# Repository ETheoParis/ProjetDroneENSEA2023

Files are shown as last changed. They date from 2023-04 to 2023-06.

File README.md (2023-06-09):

# ProjetDroneENSEA2023

I. Introduction :

Nous avons choisi de constituer un groupe de 5 personnes pour asservir et concevoir le PCB d'un drone. La structure en impression 3D nous a été fourni, nous nous sommes donc penchés sur la partie électronique et informatique.
Selon le dictionnaire Larousse, un drone "est un petit avion télécommandé utilisé pour des tâches diverses". Dans notre cas, le cahier des charges impose que notre drone puisse décoller, voler de manière rectiligne et atterrir après avoir volé pendant x mètres. 
Pour satisfaire le cahier des charges, nous avons divisé le travail entre les membres du groupe. Jack Du, Nesrine Mathlouthi, Cassandre Chandelier et Théo Paris se sont occupés de l’asservissement et du programme informatique pendant que Fannie Bichemin a réalisé le schématique  et l’éditeur de PCB ainsi que la soudure des composants.

I.1 Organisation :

Nous avons choisi de créer un groupe Messenger pour présenter nos avancées individuelles en dehors des séances de projet. Nous présentions nos recherches et les idées que nous avions pour résoudre les problèmes que nous avons rencontrés. De plus, nous avons réalisé dès la première séance un diagramme de Gantt pour suivre l’évolution de nos tâches respectives et du projet dans sa globalité. 

Que ce soit pour la surveillance de territoires, l'inspection de bâtiments, la cartographie de zones difficiles d'accès ou encore la livraison de colis, les drones sont devenus indispensables pour de nombreuses entreprises. Il s’agit de petits avions télécommandés utilisés pour des tâches diverses. (Larousse)

Notre objectif est d’asservir et de concevoir le PCB d’un drone quadcoptère dont la structure nous a été fournie. Nous veillerons à respecter le cahier des charges suivant : 
- Véhicule autonome
- Processeur sur carte-mère
- Pas de contrôle à distance  
- Code embarqué : C sur STM32
- Avancer, décoller
- Avancer "droit" puis de 10 m.

____________________________________________________________________________________________________________________________________________________________

I.1 Répartition des tâches :

Afin de satisfaire le cahier des charges, nous avons constitué un groupe de cinq personnes formé par :
- Fannie Bichemin (Hardware)
- Cassandre Chandelier, Jack Du, Nesrine Mathlouthi et Théo Paris (Asservissement et Software)

En ce qui concerne les livrables tels que le rapport et la soutenance, ils ont été complétés par les membres en expliquant les parties qui les concernent. 
____________________________________________________________________________________________________________________________________________________________

I.2 Organisation :

Afin de travailler facilement, nous avons choisi de créer un groupe Messenger. Ce dernier nous a permis de partager nos avancées individuelles en dehors des séances de projet. Nous présentions nos recherches et idées que nous avions pour résoudre les problèmes que nous avons rencontrés. De plus, nous avons réalisé dès la première séance un diagramme de Gantt pour suivre l’évolution de nos tâches respectives et du projet dans sa globalité. 

____________________________________________________________________________________________________________________________________________________________
____________________________________________________________________________________________________________________________________________________________

II.Hardware

II. Réalisation :

II.1 Le PCB :

Afin de réaliser le PCB, nous avons commencé par faire le schématique. 
Nous avons tout d’abord rassemblé toutes les datasheets et nous avons dessiné un diagramme pour visualiser le placement des composants (Cf figure.1 ) ainsi que le nombre de composants nécessaires pour concevoir le PCB. Par la suite, nous avons regardé les schémas présents dans les datasheets pour connaitre la valeurs des résistances et des condensateurs à placer autour du régulateur et des blocs moteurs. Nous nous sommes également aidés du TD concernant KiCad pour trouver les valeurs des résistances à placer autour de la carte STM32. 

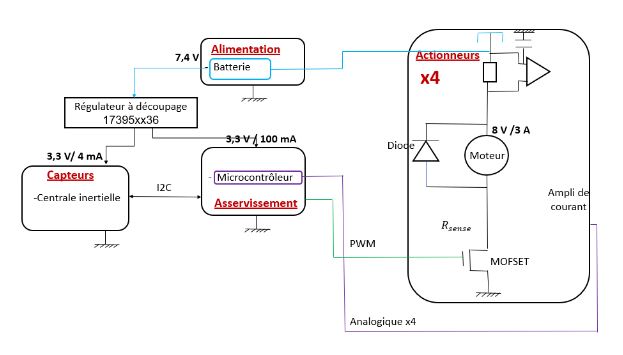
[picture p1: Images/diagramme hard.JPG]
diagramme hardware


Figure 1: Diagramme qui représente les différents éléments électroniques utilisés 

Nous avons donc abouti au schématique suivant :

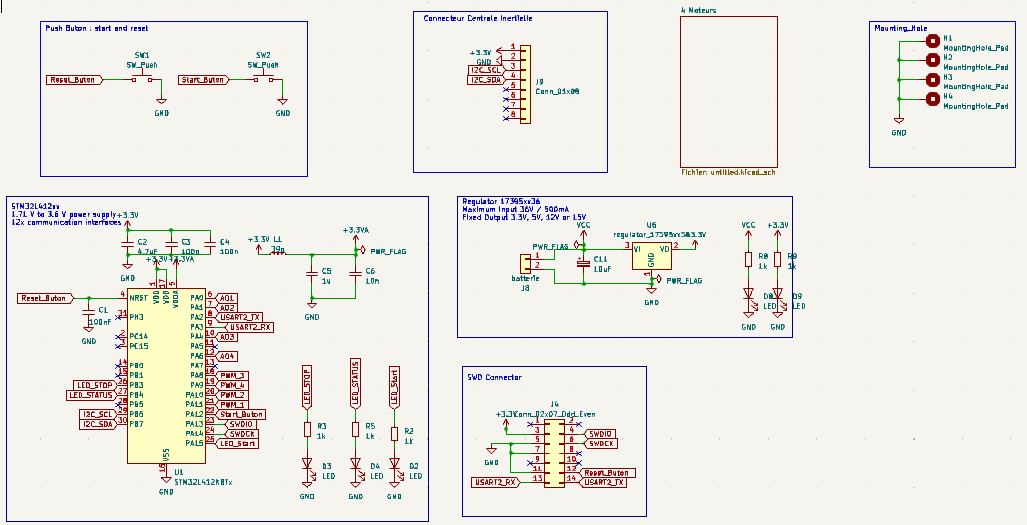
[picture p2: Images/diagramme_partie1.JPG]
schématique1


	Figure 2.a : Première partie du schématique du projet

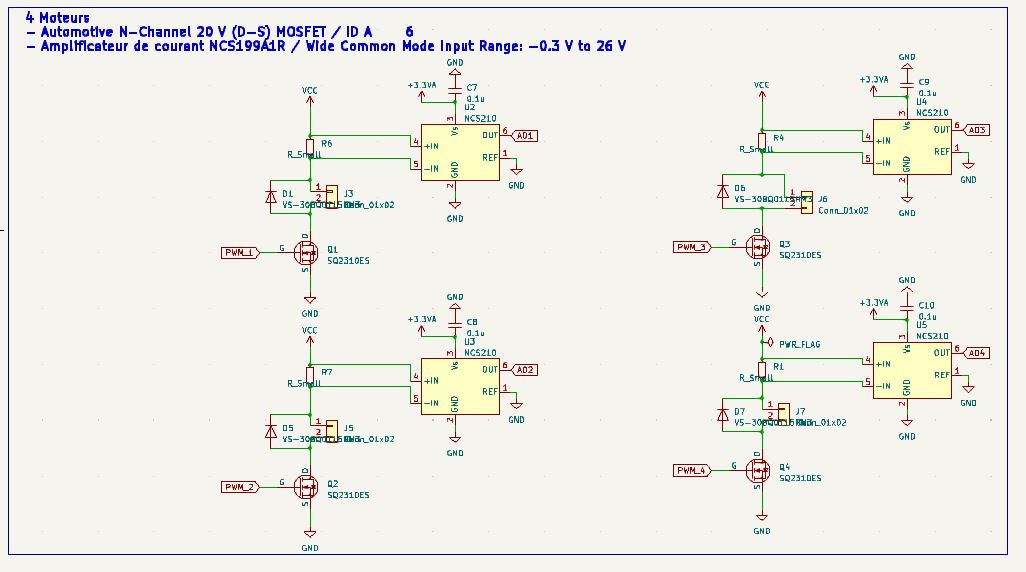
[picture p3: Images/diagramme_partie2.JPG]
diagramme partie2


Figure 2.b : Deuxième partie du schématique du projet (les moteurs)

Le schématique comporte plusieurs parties: 

-La carte STM32
-Les boutons poussoirs
-La centrale inertielle
-La cellule de régulation
-Le connecteur SWD
-La cellule des 4 moteurs 
 
Pour ajouter les résistances, les condensateurs et les bobines, nous avons regardé les montages présentés dans les datasheets. Ces montages nous permettent de connaître le nombre et la valeur des résistances et des condensateurs à placer autour des composants centraux”.
Les problèmes rencontrés sont : 
Le choix des empreintes (faire attention au numéro à prendre le numéro 0603 et “l’option” handsolder pour faciliter la soudure ; Créer des empreintes si elles n’existent pas déjà dans les librairies en faisant surtout attention aux distances entre les pads ainsi que les contours). 
Ne pas oublier de mettre des power flag.
Les empreintes des condensateurs en fonction de leurs valeurs. 

Par la suite, nous avons placé les composants sur l’éditeur PCB. Il a fallu faire en sorte que la taille et la forme du PCB soient adaptées à l’emplacement prévu sur la base du drone imprimée en 3D. 

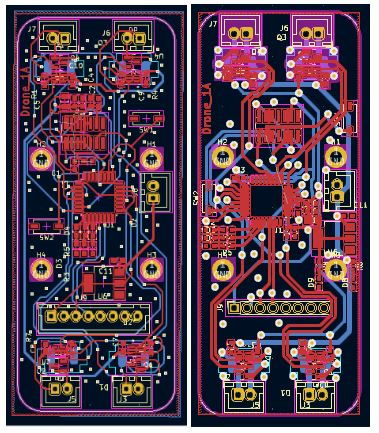
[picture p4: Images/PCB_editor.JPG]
editor PCB


Figure 2.b : PCB 

Remarques:

Le PCB de gauche est la version qui aurait dû être fabriquée par le procédé “traditionnel”.  
Le PCB de droite est celui qui a été refait par Monsieur Papazouglou car il fallait modifier la manière de placer les composants puisque le PCB a été fabriqué par le système de gravure. 

Les problèmes rencontrés sont: 
Faire en sorte de relier de la manière la plus courte possible les pads entre eux. 

____________________________________________________________________________________________________________________________________________________________

Les choses à retenir:
Multiplier par 4 le “bloc moteur” (transistor, diode, connecteur, résistance, régulateur) et utiliser les coordonnées sur Kicad pour bien aligner les 4 blocs. 
Placer les condensateurs “liés” à la carte STM32 très proches du microprocesseur. 
Ne pas oublier de mettre des vias en plus un peu partout sur le PCB.

____________________________________________________________________________________________________________________________________________________________

Enfin, nous avons soudé les composants sur le PCB : 

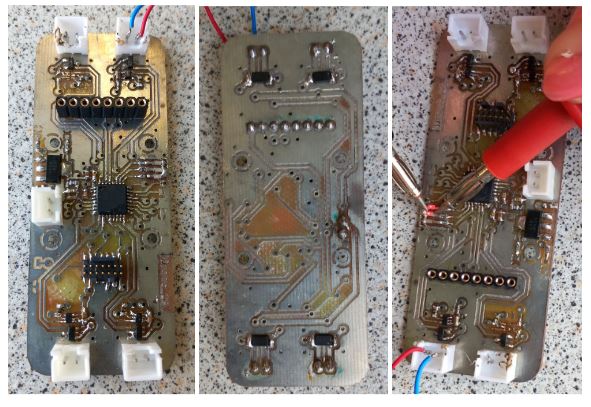
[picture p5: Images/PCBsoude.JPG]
PCB soude


Figure 3 : PCB soudé 

Remarque:
La dernière photo permet de montrer que les 3 diodes sont branchées dans le bon sens et qu’elles fonctionnent. 

Les problèmes rencontrés et les choses à retenir sont:
Mettre du flux pour éviter les courts circuits (surtout pour le microprocesseur et les composants très petits et très rapprochés).
Souder en premier les petits composants et en dernier les connecteurs (notamment pour éviter de les brûler).

____________________________________________________________________________________________________________________________________________________________

III. L’asservissement :

____________________________________________________________________________________________________________________________________________________________

III.1. Recherches préalables : 

Dans un premier temps, nous avons commencé par trouver une documentation adaptée à nos besoins. Il fut difficile de trouver des ressources pertinentes. Finalement, nous nous sommes basés principalement sur les articles suivants :

- Géométrie et commande des drones : https://www.techniques-ingenieur.fr/res/pdf/encyclopedia/42398210-s7818.pdf (1)
- State Space System Modelling of a Quad Copter UAV : https://arxiv.org/pdf/1908.07401.pdf (2)
- Cours d'asservissement de M.Haidar (3)

III.2. 1ère Modélisation : Discrétisation-Découplage 

L’objectif de cette modélisation est de réussir à déterminer notre commande u que nous pourrons exploiter par la suite via nos moteurs. 

Après avoir cherché la modélisation la plus proche de la réalité, on effectue une représentation d'état du système. On se base alors sur l'article (2) précédemment introduits. 

Nos paramètres d’entrées représentés par le vecteur X sont : 

l’accélération selon x 
l’accélération selon y
l’accélération selon z
l’accélération angulaire selon thêta 
l’accélération angulaire selon phi
l’accélération angulaire selon psi 

Nous avons basé notre premier modèle sur le document State Space System Modelling of a Quadcopter UAV qui donnait une représentation d'état du système.

Représentation d’état du système
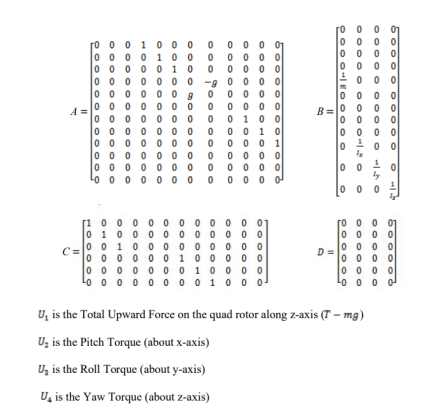
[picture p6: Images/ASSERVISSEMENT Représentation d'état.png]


Après avoir mis en forme les équations sur Matlab et défini les paramètres de l’étude, on détermine les indices relatifs en cherchant CA^rho-1 ≠ 0. 
On obtient les résultats suivants : 

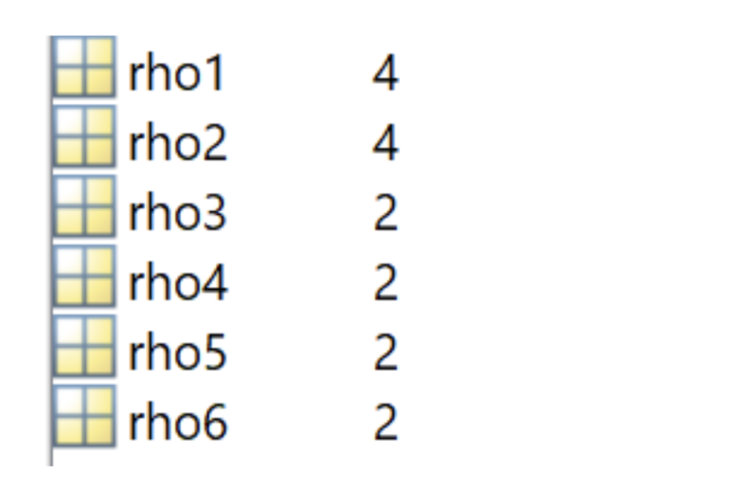
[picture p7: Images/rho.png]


On doit donc calculer les rho de chaque ligne.
Avec matlab on trouve les différent rho tel que la matrice soit inversible. Pour cela il suffit que au moins 1 des coefficient de la ligne soit non nul.
Une fois la matrice de découplage obtenu la commande est obtenu par la relation suivante.



On devrait ensuite pouvoir lier chaque commande avec la tension dans les moteurs. En effet U1 est la somme des forces, U2 le couple selon l'axe x,U3 le couple selon l'axe y,U4 le couple selon l'axe z.

On peut alors déterminer l’inverse de la matrice de découplage, on constate un problème car le système possède 4 commandes pour 6 sorties. On ne peut donc pas découpler les variables du système car le système est sous-actionné (cf cours d'asservissement).

Nous avons donc changé de modèle pour se baser sur celui de la simulation quadcopter (par Monsieur Djemai).

III. 3 Nouvelle modélisation :

On se base sur une nouvelle modélisation qui nous donne directement l'équation des couples et de la somme des forces des moteurs en fonction des accélérations. 
Il faudrait trouver un moyen de déterminer les fonctions seuil et les constants réstantes. On sait déja que mu est la force minimum des moteurs pour faire décoler de drone. Avec plus de temps il aurait surment été possible de faire fonctionner l'asservissement.

____________________________________________________________________________________________________________________________________________________________
____________________________________________________________________________________________________________________________________________________________

IV. Software :

##
Pour la partie code en C, le code sur carte NUCLEOH7A3ZI est présent sur le projet NUCLEOH7A3ZI_MPU6050. Nous n'avons pas optimisé et clarifié totalement le code suite à un problème de makefile sur les fonctions crées automatiquement par STM32 via l'ioc.
Le code a été également porté sur un autre projet (DroneFlying en l'occurence) pour le code à implémenter sur le PCB du drone.

1. PWM

En ce qui concerne le contrôle des 4 moteurs, on a décidé qu'elle se ferrait via une PWM (Pulse Width Modulation ou Modulation de largeur d'impulsion en français). 
La méthode PWM consiste à faire varier le rapport cyclique à une fréquence fixe pour ajuster la tension à la valeur cible souhaitée.

![image] 
(https://github.com/ETheoParis/ProjetDroneENSEA2023/blob/main/Images/PWM.png)

Figure 4 : PWM Fonctionnement

![image] 
(https://github.com/ETheoParis/ProjetDroneENSEA2023/blob/main/Images/PWM_Diagramme.png)

Figure 5 : Diagramme PWM 

La fréquence fixe avec laquelle nous travaillons est alors de 20kHz afin d'éviter les fréquences audibles par l'Homme.
Dans le cas de notre test sur NUCLEO, nous avons configuré un timer via l'interface ioc sur STL32CubeIDE. La fréquence d'horloge de base de la carte était de 80MHz. 
Nous avons alors ajouté un PSC (prescaler) "4-1" et un rapport de division ARR (auto reload register) de "1000-1" afin d'obtenir une fréquence d'horloge d'étude de 20kHz.

![image]
(https://github.com/ETheoParis/ProjetDroneENSEA2023/blob/main/Images/PWM_Config1.png)

![image]
(https://github.com/ETheoParis/ProjetDroneENSEA2023/blob/main/Images/PWM_Config.png)

Figure 6 & 7 : Configuration Timer pour PWM 

D'ailleurs, en ce qui concerne STM32CubeIDE, il faut penser à générer automatiquement les fichiers de code .c et .h implémentés par STM lors de l'utilisation d'un port GPIO quelconque ou bien d'un timer comme c'est le cas actuellement.
(XXX.ioc -> Project Manager -> Code Generator -> Generate peripheral initialization as a pair of '.c/.h' files per peripheral)

En ce qui concerne le fonctionnement, on doit alors déterminer une valeur de comparaison CCR afin d'avoir le rapport cyclique souhaitée. 
Dans le cas de notre code, nous avons testé avec sortie sur l'oscilloscope la PWM pour différentes valeurs de CCR choisie (200, 400, 800).

![image]
(https://github.com/ETheoParis/ProjetDroneENSEA2023/blob/main/Images/PWM_Oscilloscope.png)

Figure 8 : Test PWM sur oscilloscope

La fonction calculCCR permet de faire le lien entre une tension voulue et la PWM. Son résultat serait utilisé dans la fonction __HAL_TIM_SET_COMPARE pour changer la valeurs de la PWM.
La fonction CalculCCR n'a pas pu être vérifiée et optimisée avec les caractéristiques des moteurs (notamment la constance de couple Kc propres à nos moteurs) dans le cas de notre drone puisqu'on a eu un problème hardware sur le PCB qui a empêché les tests. Toutefois, la PWM était effectivement fonctionnel avec affichage sur l'oscilloscope. Nous aurions encore eu à optmiser le choix de CCR afin d'être bien compris dans la plage de fonctionnement des moteurs (en terme de tensions/vitesse de rotation acceptées). Cela aurait pu se faire en adoptant un ordre croissant de CCR afin d'éviter d'endommager les moteurs.

2. MPU6050

Pour contrôler la trajectoire du drone et le stabiliser, nous avons besoin d'un gyroscope et d'un accéléromètre qui permet d'obtenir des valeurs de positions et d'angle après traitement. On a donc utilisé une centrale inertielle qui comprend les deux : le MPU6050.
Cette centrale inertielle communique en bus I2C avec le microprocesseur et transmet les données via UART. On définit les ports de transmissions directement sur l'ioc, comme avec la PWM. On a donc également pu se reposer sur les bibliothèques HAL et UART déjà intégrée et propres à STM32.

Pour la récupération des données de la centrale inertielle on utilise HAL_TIM_PeriodElapsedCallback pour échantillonner la récupération des données à la fréquence du timer. Les données sont lues par HAL_I2C_Mem_Read puis enregistrées dans Rec_Data et recopier dans x, y, z. HAL_UART_Transmit permet de tester le fonctionnement du MPU en récupérant les données via une interface d'affichage tel que Putty sur Windows.

![image]
(https://github.com/ETheoParis/ProjetDroneENSEA2023/blob/main/Images/Putty.png)

Figure 9 : Affichage des valeurs d'accélération et de vitesse angulaire obtenues de la centrale inertielle sur Putty.

Toutefois, en ce qui concerne les valeurs, on observe une variation en l'absence même de mouvement. Cela est problématique par rapport au fait que l'on intègre 2 fois pour obtenir la position, on aurait dans ce cas beaucoup trop d'incertitudes et de variations par rapport à la réalité au fur et à mesure que le drone vole et se déplace. 
Il faut donc travailler sur l'échelle de précision du capteur mais nous n'avons pas pu améliorer ce point-ci par manque de temps. Nous aurions également pu filtrer les valeurs et ne garder que celles qui étaient pertinentes.

3. Fonctions intermédiaires

Nous avons également crée des fonctions intermédiaires qu'on aurait été appelé à utiliser dans le cas du déplacement de drone, toutefois, comme nous étions assez occupé par l'asservissement et l'optimisation des autres parties, nous n'avons pas pu aboutir à un stade où nous utilisions ces fonctions.

int calculVitesse1D(int acceleration, int vitesseActuelle, int pas);
void primitive(VECTEUR* derivee, VECTEUR* constante,VECTEUR* primitive, int pas);
void calculVitesse(VECTEUR* acceleration,VECTEUR* vitesseActuelle,VECTEUR* nouvelleVitesse, int pas);
void calculPosition(VECTEUR* vitesse,VECTEUR* positionActuelle,VECTEUR* nouvellePosition,int pas);
int calculCourantMoteur(int reg);
void recopie(VECTEUR * nouveau, VECTEUR * ancien);

4. Optimisation

Pour éviter que le drone ne se pose trop violemment/rapidement, ce qui aurait endommagé les composants, nous aurions pu mesurer et vérifier la variation de résistance vis-à-vis de la rotation des hélices de chaque moteur. Une résistance plus faible aurait témoigné du fait qu'il y a une réaction normale de pousée vis-à-vis du sol et donc cela aurait signifié une proximité plus importante avec le sol.

La fonction calculCourantMoteur utilise la tension au borne de la résistance Rshunt pour calculer le courant dans le moteur. Son résultat devait servir à mesurer la distance avec le sol. Bien que nous avons bien ajouté une résistance pour cette optimisation, nous n'avons malheureusement pas pu l'implémenter et la tester en plus du cahier des charges initial par manque de temps et contraintes techniques.

_______________________________________________________________________

En terme d'optimisation, on aurait également pu améliorer le code et diminuer son empreinte en terme de ressources inutiles, notamment dans le call de fonctions bien qu'on travaille déjà en C, langage avec une empreinte assez faible.
Le code aurait également pu être amélioré dans son agencement si nous avions réglé le problème d'un MakeFile affecté.

_______________________________________________________________________
_____________________________________________________________________________________

QUESTIONS OBJECTIFS DEVELOPPEMENT DURABLE:
_____________________________________________________________________________________________________________________________________
=> Quelle réflexion avez-vous mené au cours de ce projet autour de la limitation de la consommation d'énergie ?

Notre drone a été modélisé tout en prenant en compte la limitation de la consommation d'énergie. Les critères pris en compte sont :

- Le choix des composants (développé dans la question suivante) qui doit favoriser l'économie d'énergie. (batterie avec bonne capacité et poids raisonnable)

- La conception du drone (favorisation des matériaux légers pour la structure=> réduction du poids total=> travail plus efficace du moteur et aérodynamique du drone étudiée et donc une autonomie accrûe -> Apporte de nouvelles fonctionnalités qui n'étaient pas possibles)

- Usage de technologies avancées (centrale inertielle qui regroupe à la fois un accéléromètre mais aussi un gyroscope. Nous avons donc l'échange de toutes les données externes via seulement une interface I2C et évite de multiplier le nombre de composants sur le PCB qui alourdi le drone et donc augmente la consommation d'énergie et code avec un langage de bas niveau, C, donc à plutôt faible empreinte carbone).

_____________________________________________________________________________________________________________________________________
=>Expliquer les critères de choix des composants de votre projet (critères environnementaux, de disponibilité, d'emprise spatiale, autres).

Le choix des composants est primordial lors de la réalisation d'un projet. Il existe plusieurs critères à prendre en considération:

-Critères environnementaux : Il faut effectivement privilégier le fait d'utiliser le moins de composants possibles sur notre PCB et sinon utiliser ceux qui présente une efficience importante en terme de consommation.

-Critères de disponibilité : Il est nécessaire de privilégier les composants des fournisseurs les plus fiables (Farnell/RS/Mouser/Digikey/Gotronic...). Chez ces derniers, le choix de matériel est largement plus important et des datasheets des composants y sont proposées.

-Critères d'emprise spatiale : (taille et poids : les composants trop lourds peuvent avoir un impact négatif sur les caractéristiques de vol du drone)

On peut également prendre en compte les critères suivants : le coût/les performances et la compatibilité avec d'autres composants du système. 

Concentrons-nous désormais sur chaque composant : 
- Batterie : Nous avons choisi une batterie de capacité 3,7 Wh avec une masse = 30g afin de respecter les critères d'emprise spatiale.La capacité a été choisie afin de permettre le respect du cahier des charges (vol sur 10m avec montée et descente) sans trop impacter l'autonomie (puisque la charge influe sur la vitesse de rotation des hélices pour maintenir le drone en vol).

- Régulateur de tension (17395xx36): Notre choix de composant présente une efficité maximale de 97%. Cela est bien plus pertinent dans le cas d'un drone avec un accumulateur de faible capacité qu'un régulateur linéaire/LDO qui présente une efficacité maximale moindre.

D'ailleurs, la différence d'efficacité entre un régulateur linéaire et un régulateur à découpage s'explique par leur fonctionnement différent :
Les régulateurs linéaires, tels que les régulateurs de type LDO (Low Drop-Out), fonctionnent en utilisant une configuration de transistors pour réguler la tension de sortie. Ils offrent une sortie stable et régulée, mais la différence de tension entre l'entrée et la sortie (la "chute de tension" ou "drop-out") entraîne une dissipation de puissance importante sous forme de chaleur.  (R*I^2) Cela signifie que les régulateurs linéaires ont une efficacité relativement faible, surtout lorsque la différence de tension entre l'entrée et la sortie est élevée. 

En revanche, les régulateurs à découpage fonctionnent en commutant rapidement entre un état actif et un état inactif pour maintenir une tension de sortie régulée. Ils utilisent des inductances et des condensateurs pour stocker et transférer l'énergie de manière efficace. Les régulateurs à découpage sont capables de convertir l'énergie de manière beaucoup plus efficace que les régulateurs linéaires, car ils minimisent les pertes de puissance sous forme de chaleur. Cela se traduit par une meilleure efficacité énergétique et une dissipation de chaleur réduite.

- Moteur: Les critères pris en compte sont principalement la consommation, la taille, la puissance délivrée, le poids et la vitesse (rpm(tr/min) = constante de vélocité * tension. Le rpm va influencer sur la stabilité du vol. Plus celui-ci est faible, plus le vol sera stable). Notre choix s'est porté sur Moteurs Brossés Axe 1.0mm pour Quadricoptère Tiny 8X RC.

- Hélices: Nous prenons en considération leurs longueurs, leurs pas ainsi que leurs compositions (matériaux).

- Châssis: Nous utilisons un châssis qui est fait en PLA, l'acide polylactique qui est en plastique biodégradable (sous certaines conditions) et recyclable par extrudeuse (le plus simple et moins couteux) ou bien par dépolymérisation et repolymérisation. Il s'agit d'un matériau à faible empreinte carbone, notamment dans le cas d'un prototypage comme on est ammené à faire, il s'agit d'une bonne solution logistique et environnemental. 
_____________________________________________________________________________________________________________________________________
=> Sources :

-Datasheets des composants 
-https://www.pilgrim-technology.com/drones-et-environnement/

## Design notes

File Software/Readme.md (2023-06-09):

BE CAREFUL !!
DroneFlying is the project to implement on the drone's PCB.*

NUCLEO_H7A3ZI_MPU6050 is the one coded to test it firstly on our NUCLEO board.

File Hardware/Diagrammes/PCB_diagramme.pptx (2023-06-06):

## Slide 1

Alimentation

- Batterie

X64022S1P

Actionneurs

- Moteurs
- Hélices

Tiny 8X RC Drone

Capteurs

- Centrale inertielle

MPU6050

BETAFPV

Asservissement

- Microcontrôleur

STM32L412KB

Autres composants:

- Régulateur (à découpage)
- Diodes
- Transistor MOSFET
- Ampli de mesure de courant

17395xx36

VS-30BQ0115HM3

NCS199A3RSQT2G

SQ2310ES

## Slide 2

7,4 V

Alimentation

- Batterie

Actionneurs

x4

Régulateur à découpage
17395xx36

3,3 V / 100 mA

- Microcontrôleur

Asservissement

8 V /3 A

3,3 V/ 4 mA

Analogique

Diode

Moteur

Capteurs

-Centrale inertielle

I2C

Ampli de courant

R_(sense)

PWM

MOSFET

Analogique x4

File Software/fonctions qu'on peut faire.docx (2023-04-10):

- Fonction main.c
- Fonction tick (void) → durée entre tick et tock

Calcul le temps présent à chaque fonction. Permet de déterminer la vitesse et la position du drone.

- Fonction perturbationsExt (perturbations en entrée, à déterminer) →

Permet de prendre en compte les perturbations extérieures (s’il y en a)

- Fonction asservissement (vitesse actuelle) → sortie = void, changement direct de la vitesse, agir sur fonction tensionMoteur

Permet d’adapter la vitesse du drone en agissant directement sur les fonctions en rouges, en adaptant la tension du moteur.

- Fonction deplacement (vitesseActuelle, vitesseAttendue) → void, changement direct de la vitesse par tensionMoteur

Permet de faire avancer le drone dans la direction que l’on souhaite (x +=1 ou x-=1)

- Fonction altitude (position, altitudeMax, tensionMoteur) → void, changement direct altitude

Permet de faire monter ou descendre le drone selon le sens souhaité (y +=1 ou y-=1)

- Fonction vitesseActuelle

Permet de calculer la vitesse du drone

- Fonction vitesseAttendue (vitesse souhaitée) → void

Permet d’avoir la vitesse référence, celle à ne pas dépasser (choisie par nous, modifiable)

- Fonction tensionMoteur

Permet d’adapter la tension des moteurs, contrôlant ainsi la vitesse du drône

- Fonction altitudeVoulue (altitude souhaitée) → void

Permet d’avoir l’altitude de référence, celle à atteindre

- Fonction position (tick, vitesse du drone, altitude)

Permet d’avoir la position du drone à l’instant t)

Attention, on peut supprimer les fonctions altitudeVoulue et vitesseAttendue pour faire un #define.

On créerait des variables globales : ALTITUDE_MAX, ALTITUDE_MIN, VITESSE_MAX dans tout le programme, et faire appel à ces variables dans les arguments des fonctions. Ce sera peut-être mieux.

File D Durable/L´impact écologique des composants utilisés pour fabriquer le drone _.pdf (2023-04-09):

L'impact écologique des composants utilisés pour fabriquer le drone

La Batterie :
-Sa taille et son poids
-Sa capacité (affecte la durée de vol du drone, i.e. son autonomie, ainsi que son poids). Plus la capacité est élevée, plus la batterie sera lourde et plus il faudra que la force de xxxxx soit grande pour que le drone s´envole.
Sa charge: le temps de charge est important en fonction de l'utilisation du drone.

Le moteur :
-Sa consommation: celle-ci aura un impact sur l’autonomie de la batterie.
-Sa taille
-Sa puissance délivrée
-Sa vitesse: rpm (tr/min)= constante de vélocité * tension. Le rpm va influencer la stabilité du vol. Plus celui-ci est faible, plus le vol sera stable.

Les hélices:
-Sa composition (les matériaux) influe sur le poids
-Sa longueur et son pas : elle influence la vitesse, la stabilité du vol

Le châssis :
En PLA, acide polylactique, un plastique biodégradable et recyclable

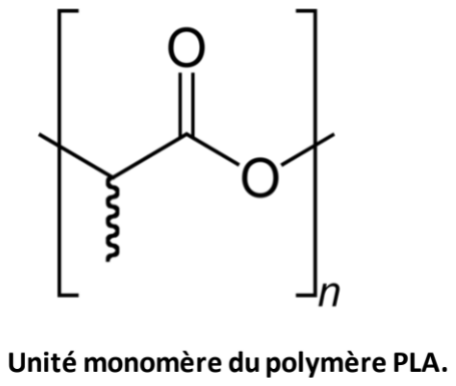
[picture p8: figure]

- Recyclage par compostage industriel avec conditions particulières (T > 60°C)
- Par une extrudeuse
- dépolymérisation par transestérification
-> Impact environnemental plutôt faible!

https://www.pilgrim-technology.com/drones-et-environnement/

| Comp osants
ALIME NTATI ON | Batteri e X6402 2S1P
CAPT EURS | Centra le inertiel le MPU6 050
ASSE RVISS EMEN T | Microc ontrole ur STM3 2L412 KB
ACTIO NNEU RS | Moteur Tiny 8X RC Drone
| Hache ur
| Hélice s BETA FPV

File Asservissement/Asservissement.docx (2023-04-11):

Modélisation drône :

Système : Drône

Référentiel (R0) : sol

entrées : accélération du centre du système et vecteur R correspondant à l’orientation

vecteur d’état : vecteur position p=(px,py,pz) / vitesse du système / R

Fonctionnement :

Le drone possède quatre propulseurs qui peuvent être commandés indépendamment. Ces actionneurs vont permettre de réguler l’attitude et la position. Pour ce type de drone, on distingue classiquement quatre mouvements possibles : les gaz, le lacet, le roulis et le tangage.

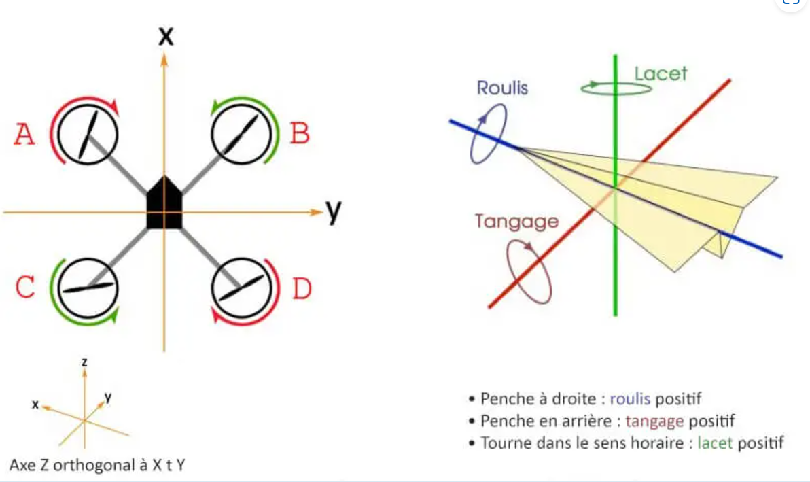
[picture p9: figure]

Pour garder le contrôle du lacet, il faut deux hélices qui tournent dans le sens horaire (hélice à pas normal) et les deux autres dans le sens antihoraire (hélices à pas inversé). Le drone possède six propulseurs. Il peut pourtant être considéré comme un quadrirotor car tous ses propulseurs ont une direction verticale.

EQUATIONS DU DRONE :

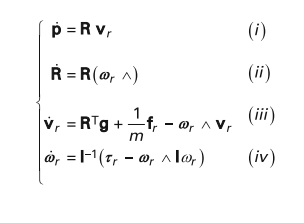
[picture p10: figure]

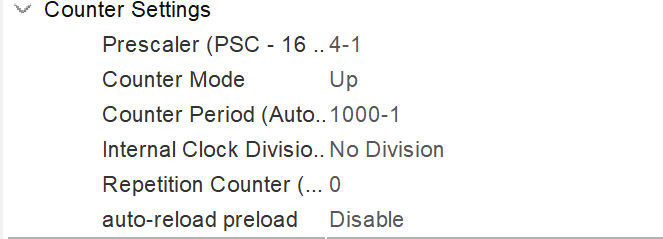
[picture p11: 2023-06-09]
Images/PWM_Config.png

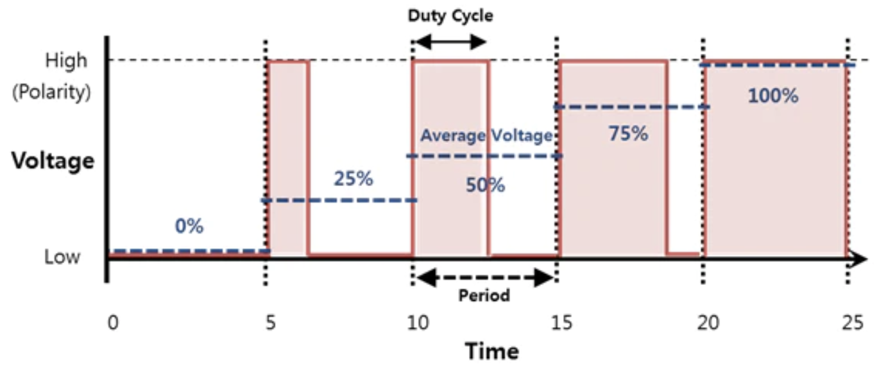
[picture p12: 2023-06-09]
Images/PWM.png

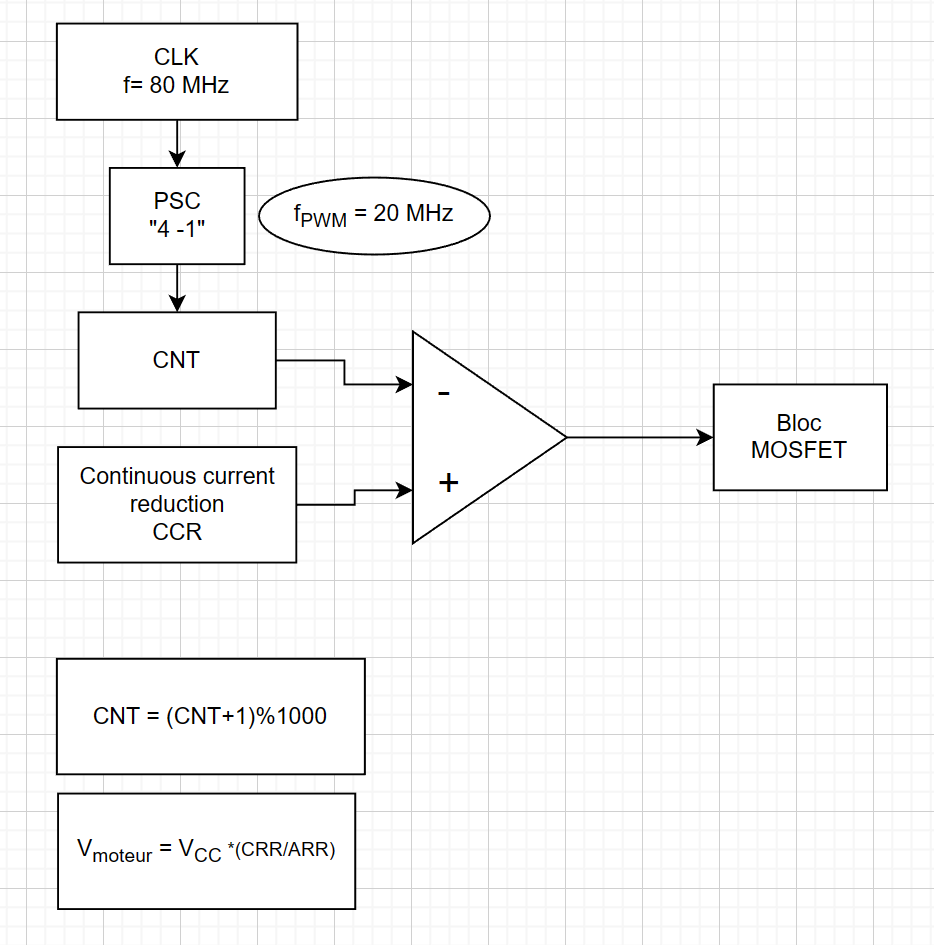
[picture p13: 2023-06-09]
Images/PWM_Diagramme.png

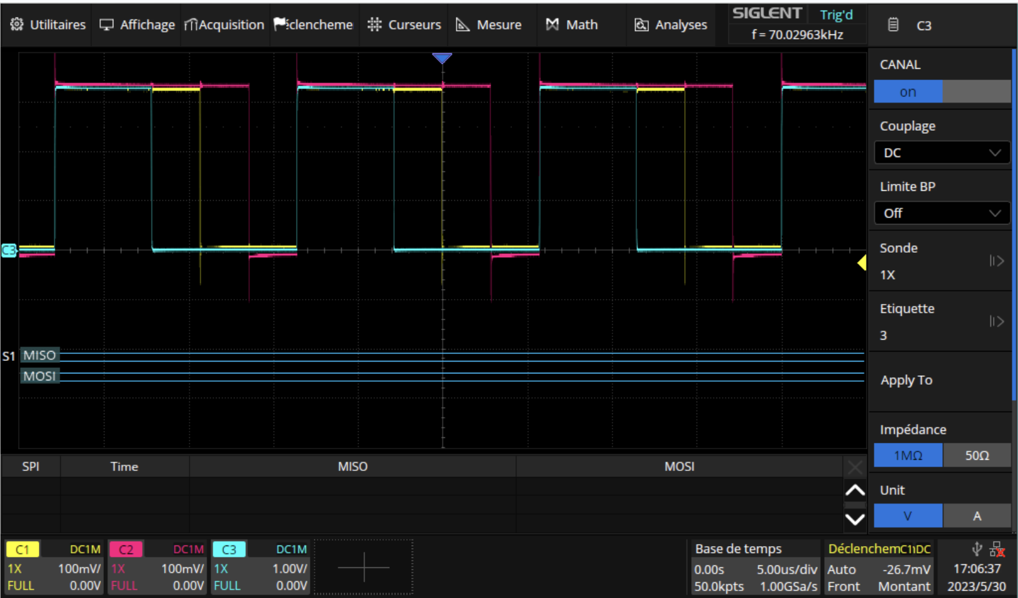
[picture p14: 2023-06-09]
Images/PWM_Oscilloscope.png

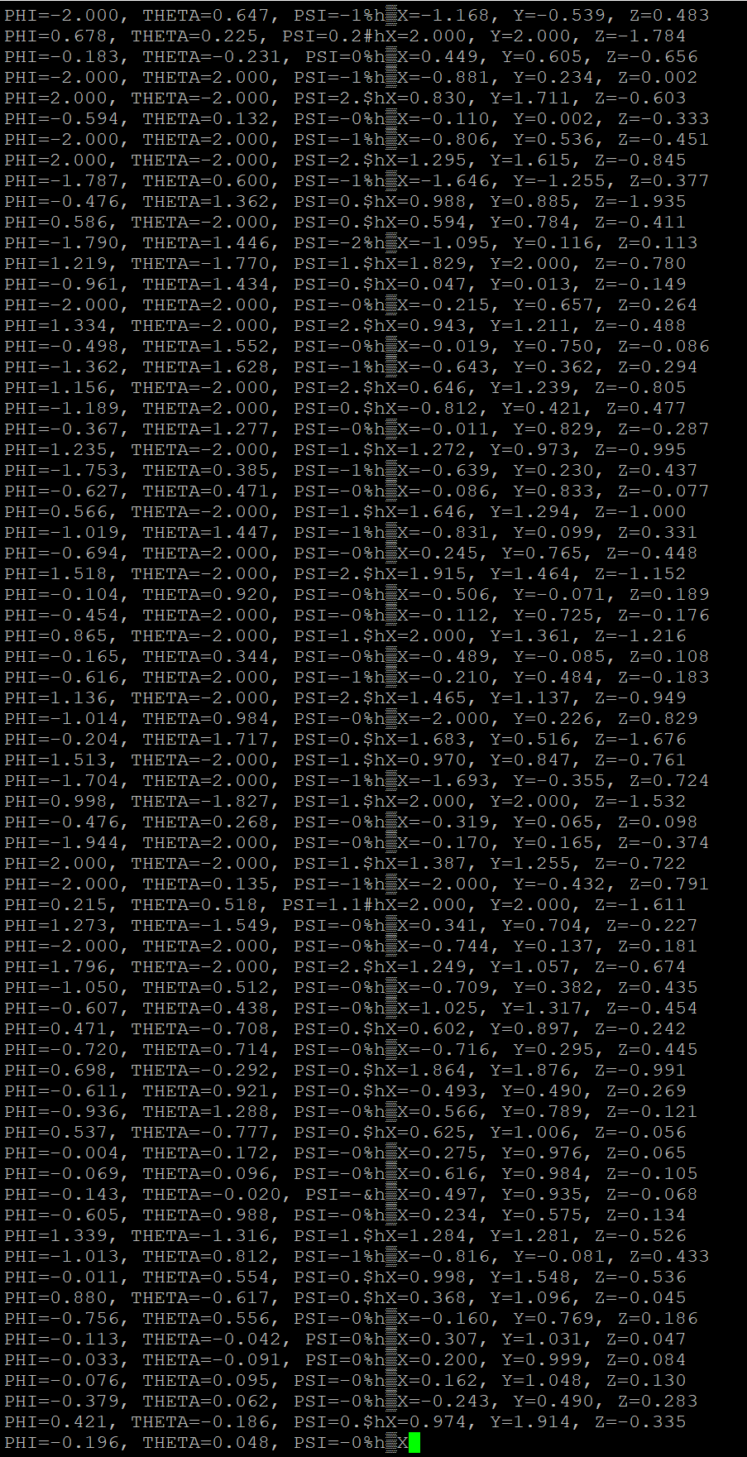
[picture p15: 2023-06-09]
Images/Putty.png

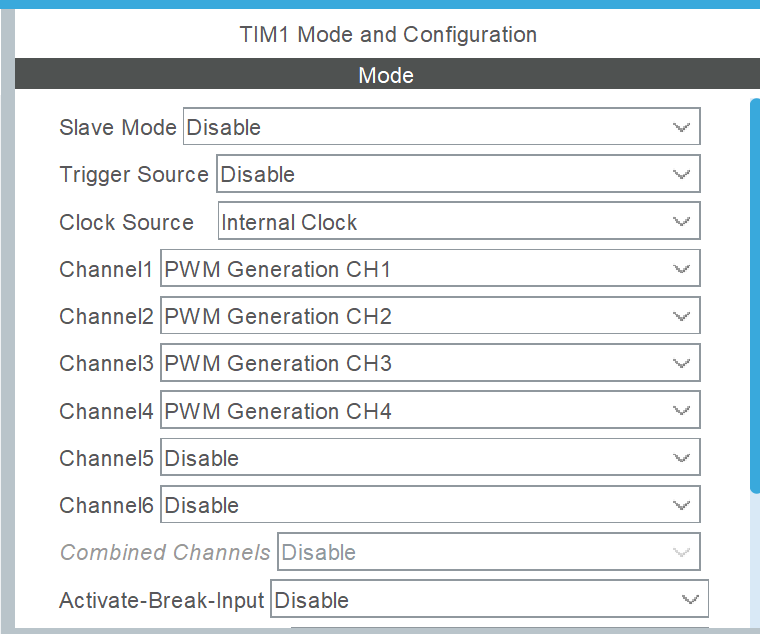
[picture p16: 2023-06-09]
Images/PWM_Config1.png

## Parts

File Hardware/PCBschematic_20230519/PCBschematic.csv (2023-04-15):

Source: | C:\Users\fanni\Documents\2022-2023\S6\Projet\ProjetDroneENSEA2023\PCBschematic\PCBschematic.kicad_sch
Date: | 14/04/2023 22:20:29
Tool: | Eeschema (7.0.0)
Generator: | C:\Users\fanni\Documents\logiciels_instales\7.0\bin\scripting\plugins/bom_csv_grouped_by_value.py
Component Count: | 49
Collated Components:
Item | Qty | Reference(s) | Value | LibPart | Footprint | Datasheet | DNP | Sim.Device | Sim.Pins | Sim.Type
1 | 1 | C1 | 100nF | Device:C_Small | Capacitor_SMD:C_0603_1608Metric_Pad1.08x0.95mm_HandSolder | ~
2 | 1 | C2 | 4.7uF | Device:C_Small | Capacitor_SMD:C_0603_1608Metric_Pad1.08x0.95mm_HandSolder | ~
3 | 2 | C3, C4 | 100n | Device:C_Small | Capacitor_SMD:C_0603_1608Metric_Pad1.08x0.95mm_HandSolder | ~
4 | 1 | C5 | 1u | Device:C_Small | Capacitor_SMD:C_0603_1608Metric_Pad1.08x0.95mm_HandSolder | ~
5 | 1 | C6 | 10n | Device:C_Small | Capacitor_SMD:C_0603_1608Metric_Pad1.08x0.95mm_HandSolder | ~
6 | 3 | C7, C9, C10 | 0.1 | Device:C_Small | Capacitor_SMD:C_0603_1608Metric_Pad1.08x0.95mm_HandSolder | ~
7 | 1 | C8 | 0.1u | Device:C_Small | Capacitor_SMD:C_0603_1608Metric_Pad1.08x0.95mm_HandSolder | ~
8 | 1 | C11 | 200u | Device:C_Small | Capacitor_SMD:C_0603_1608Metric_Pad1.08x0.95mm_HandSolder | ~
9 | 1 | D1 | VS-30BQ0115HM3 | Diode:1N5400 | Diode_SMD:D_0603_1608Metric_Pad1.05x0.95mm_HandSolder | http://www.vishay.com/docs/88516/1n5400.pdf |  |  | D | 1=K 2=A
10 | 3 | D2, D3, D4 | LED | Device:LED | LED_SMD:LED_0603_1608Metric_Pad1.05x0.95mm_HandSolder | ~
11 | 3 | D5, D6, D7 | VS-30BQ0115HM3 | Diode:1N5400 | Diode_SMD:D_0201_0603Metric_Pad0.64x0.40mm_HandSolder | http://www.vishay.com/docs/88516/1n5400.pdf |  |  | D | 1=K 2=A
12 | 4 | H1, H2, H3, H4 | MountingHole_Pad | Mechanical:MountingHole_Pad | MountingHole:MountingHole_3.2mm_M3_DIN965_Pad | ~
13 | 4 | J3, J5, J6, J7 | Conn_01x02 | Connector_Generic:Conn_01x02 | Connector_JST:JST_XH_B2B-XH-A_1x02_P2.50mm_Vertical | ~
14 | 1 | J4 | Conn_02x07_Odd_Even | Connector_Generic:Conn_02x07_Odd_Even | Connector_Molex:Molex_Micro-Fit_3.0_43045-1612_2x08_P3.00mm_Vertical | ~
15 | 1 | J8 | batterie_regulation_centraleinertielle | Connector_Generic:Conn_01x02 | Connector_JST:JST_XH_B2B-XH-A_1x02_P2.50mm_Vertical | ~
16 | 1 | J9 | Conn_01x08 | Connector_Generic:Conn_01x08 | Connector_JST:JST_XH_B8B-XH-A_1x08_P2.50mm_Vertical | ~
17 | 1 | L1 | 39n | Device:L_Small | Inductor_SMD:L_0805_2012Metric_Pad1.15x1.40mm_HandSolder | ~
18 | 4 | Q1, Q2, Q3, Q4 | SQ2310ES | Simulation_SPICE:NMOS | Transistor_Power_Module:Littelfuse_Package_H_XBN2MM | https://ngspice.sourceforge.io/docs/ngspice-manual.pdf |  |  | NMOS | 1=D 2=G 3=S | VDMOS
19 | 4 | R1, R6, R7, R8 | R_Small | Device:R_Small | Resistor_SMD:R_0603_1608Metric_Pad0.98x0.95mm_HandSolder | ~
20 | 3 | R2, R3, R5 | 1k | Device:R_Small | Resistor_SMD:R_0603_1608Metric_Pad0.98x0.95mm_HandSolder | ~
21 | 2 | SW1, SW2 | SW_Push | Switch:SW_Push | Button_Switch_THT:SW_Push_1P2T_Vertical_E-Switch_800UDP8P1A1M6 | ~
22 | 1 | U1 | STM32L412KBTx | MCU_ST_STM32L4:STM32L412KBTx | Package_QFP:LQFP-32_7x7mm_P0.8mm | https://www.st.com/resource/en/datasheet/stm32l412kb.pdf
23 | 4 | U2, U3, U4, U5 | NCS210 | Amplifier_Current:NCS210 | Package_TO_SOT_SMD:SOT-363_SC-70-6 | https://www.onsemi.com/pub/Collateral/NCS210R-D.PDF
24 | 1 | U6 | regulator_17395xx36 | Regulator_Linear:AMS1117-3.3 | Package_TO_SOT_SMD:SOT-223-3_TabPin2 | http://www.advanced-monolithic.com/pdf/ds1117.pdf

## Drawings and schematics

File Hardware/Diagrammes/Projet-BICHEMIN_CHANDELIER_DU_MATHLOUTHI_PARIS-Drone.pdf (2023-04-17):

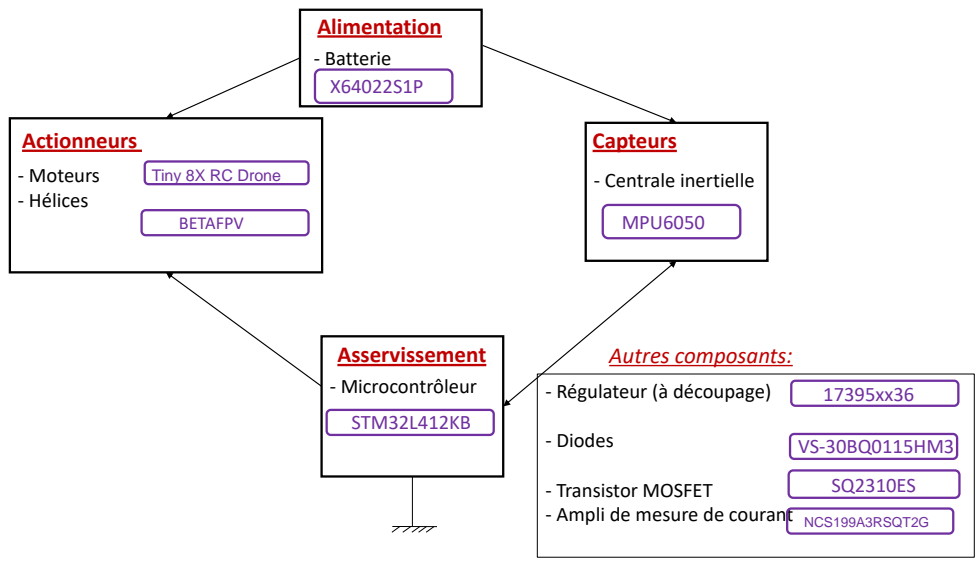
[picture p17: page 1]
- Régulateur (à découpage); - Diodes; Autres composants:; - Microcontrôleur; Actionneurs; - Batterie; Alimentation; Capteurs; - Moteurs; - Centrale inertielle; - Hélices; MPU6050; STM32L412KB; BETAFPV; NCS199A3RSQT2G; Asservissement

Tiny 8X RC Drone

- Transistor MOSFET
- Ampli de mesure de courant

x4

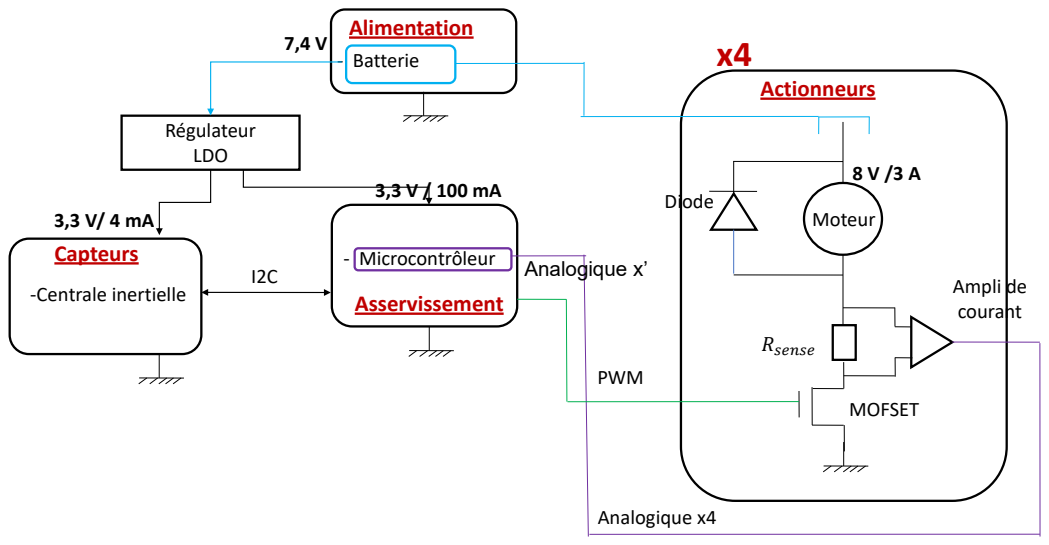
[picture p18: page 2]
Asservissement; - Microcontrôleur; Actionneurs; Moteur; Rsense; Analogique x’; Alimentation; - Batterie; Capteurs; -Centrale inertielle; Régulateur LDO; Analogique x4; PWM; Ampli de courant; Diode; MOFSET

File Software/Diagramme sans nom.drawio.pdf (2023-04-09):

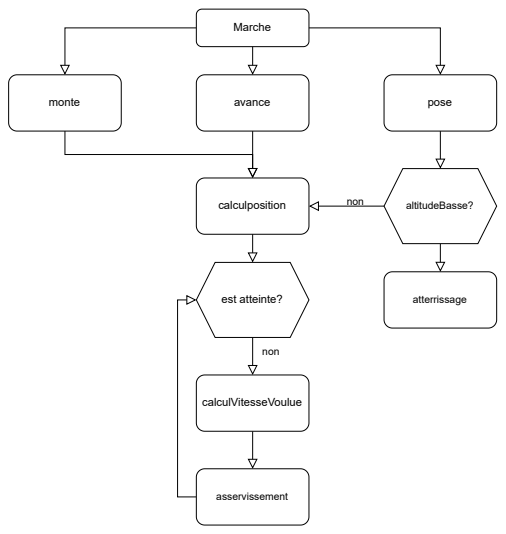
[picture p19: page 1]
Marche; monte; avance; pose; est atteinte?; calculposition; calculVitesseVoulue; non; asservissement; altitudeBasse? non; atterrissage

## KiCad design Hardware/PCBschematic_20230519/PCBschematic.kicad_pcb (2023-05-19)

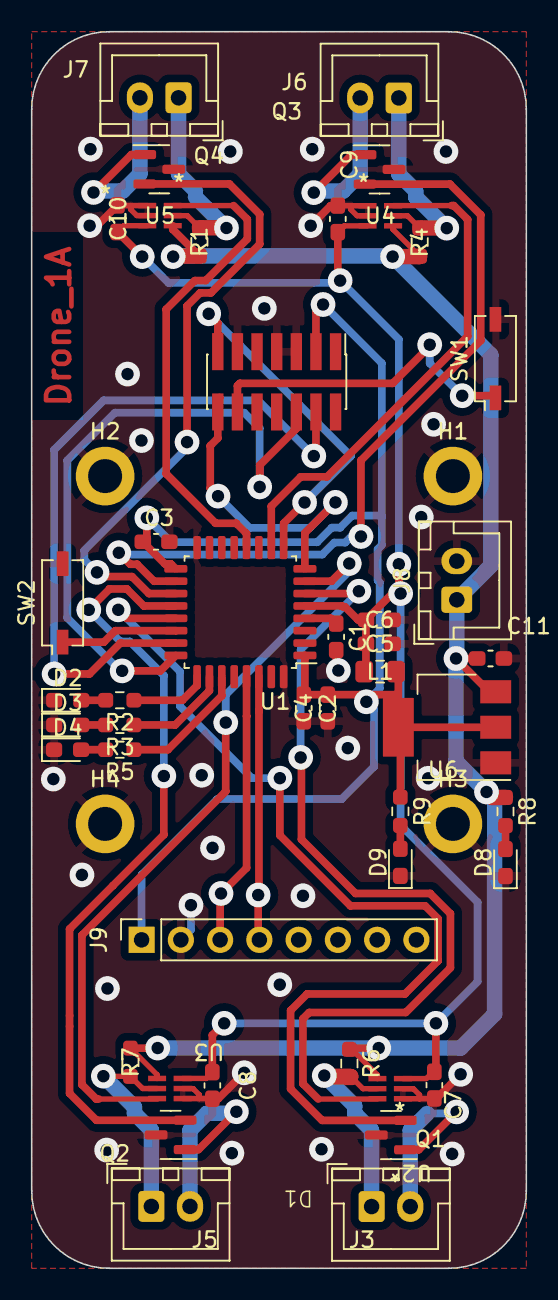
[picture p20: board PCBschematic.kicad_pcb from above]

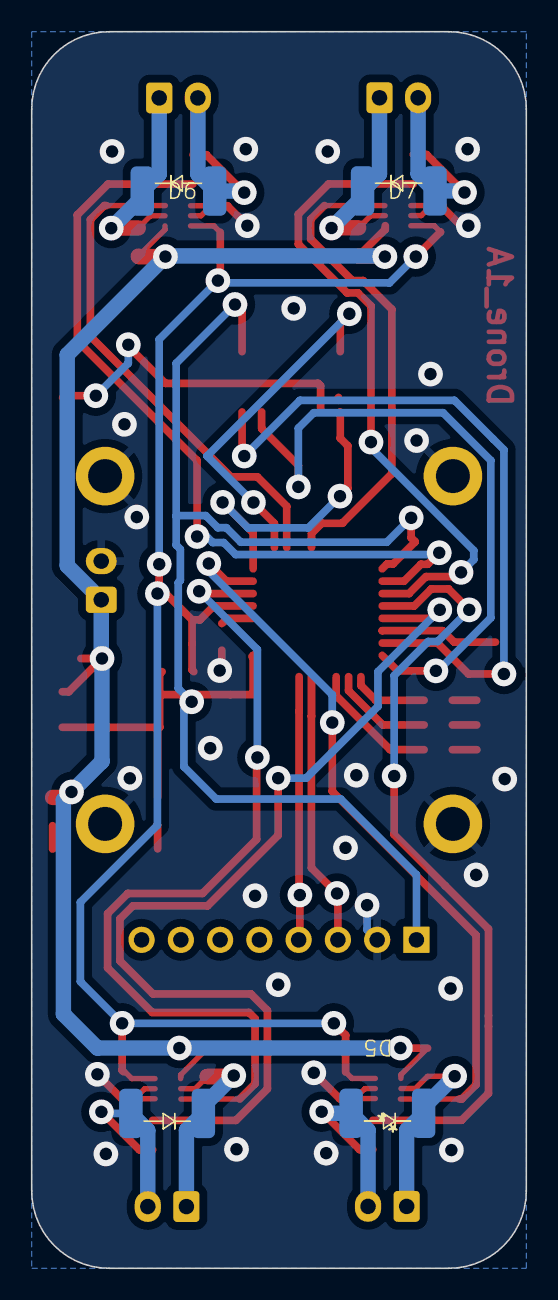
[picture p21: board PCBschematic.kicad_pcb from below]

Board: 2 copper layers, 32.0 x 80.0 mm, 53 parts (4 on the bottom side), 36 nets.

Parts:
C1: 100nF; C_0603_1608Metric_Pad1.08x0.95mm_HandSolder
C2: 4.7uF; C_0603_1608Metric_Pad1.08x0.95mm_HandSolder
C3, C4: 100n; C_0603_1608Metric_Pad1.08x0.95mm_HandSolder
C5: 1u; C_0603_1608Metric_Pad1.08x0.95mm_HandSolder
C6: 10n; C_0603_1608Metric_Pad1.08x0.95mm_HandSolder
C7, C8, C9, C10: 0.1u; C_0603_1608Metric_Pad1.08x0.95mm_HandSolder
C11: 10uF; C_0603_1608Metric_Pad1.08x0.95mm_HandSolder
D1, D5, D6, D7: VS-30BQ0115HM3; DiodeVS-30BQ015HM3
D2, D3, D4, D8, D9: LED; LED_0603_1608Metric_Pad1.05x0.95mm_HandSolder
H1, H2, H3, H4: MountingHole_Pad; MountingHole_2.2mm_M2_DIN965_Pad
J3, J5, J6, J7: Conn_01x02; JST_XH_B2B-XH-A_1x02_P2.50mm_Vertical
J4: Conn_02x07_Odd_Even; PinHeader_2x07_P1.27mm_Vertical_SMD
J8: batterie; JST_XH_B2B-XH-A_1x02_P2.50mm_Vertical
J9: Conn_01x08; PinSocket_1x08_P2.54mm_Vertical
L1: 39n; L_0805_2012Metric_Pad1.15x1.40mm_HandSolder
Q1, Q2, Q3, Q4: SQ2310ES; SOT-23
R1, R4, R6, R7: R_Small; R_0603_1608Metric_Pad0.98x0.95mm_HandSolder
R2, R3, R5, R8, R9: 1k; R_0603_1608Metric_Pad0.98x0.95mm_HandSolder
SW1, SW2: SW_Push; SW_DIP_SPSTx01_Slide_Copal_CHS-01A_W5.08mm_P1.27mm_JPin
U1: STM32L412KBTx; LQFP-32_7x7mm_P0.8mm
U2, U3, U4, U5: NCS210; SC70-6_ONS
U6: regulator_17395xx36; SOT-223-3_TabPin2

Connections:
+3.3V: C2.1, C3.1, C4.1, J4.3, J9.1, L1.1, R9.1, U1.1 (VDD), U1.17 (VDD), U6.2 (VO)
+3.3VA: C5.1, C6.1, C7.2, C8.2, C9.2, C10.2, L1.2, U1.5 (VDDA), U2.3 (Vs), U3.3 (Vs), U4.3 (Vs), U5.3 (Vs)
AO1: U1.6 (PA0), U2.6 (OUT)
AO2: U1.7 (PA1), U3.6 (OUT)
AO3: U1.10 (PA4), U4.6 (OUT)
AO4: U1.12 (PA6), U5.6 (OUT)
GND: C1.2, C2.2, C3.2, C4.2, C5.2, C6.2, C7.1, C8.1, C9.1, C10.1, C11.2, D2.1 (K), D3.1 (K), D4.1 (K), D8.1 (K), D9.1 (K), H1.1, H2.1, H3.1, H4.1, J4.5, J4.7, J4.11, J8.2, J9.2, Q1.3 (S), Q2.3 (S), Q3.3 (S), Q4.3 (S), SW1.2, SW2.2, U1.16 (VSS), U1.32 (VSS), U2.1 (REF), U2.2 (GND), U3.1 (REF), U3.2 (GND), U4.1 (REF), U4.2 (GND), U5.1 (REF), U5.2 (GND), U6.1 (GND)
I2C_SCL: J9.3, U1.29 (PB6)
I2C_SDA: J9.4, U1.30 (PB7)
LED_STATUS: R5.1, U1.27 (PB4)
LED_STOP: R3.1, U1.26 (PB3)
LED_Start: R2.1, U1.25 (PA15)
unnamed: D1.2 (A), J3.2, Q1.1 (D)
unnamed: D1.1 (K), J3.1, R6.2, U2.5 (-IN)
unnamed: D2.2 (A), R2.2
unnamed: D3.2 (A), R3.2
unnamed: D4.2 (A), R5.2
unnamed: D5.2 (A), J5.2, Q2.1 (D)
unnamed: D5.1 (K), J5.1, R7.2, U3.5 (-IN)
unnamed: D6.2 (A), J6.2, Q3.1 (D)
unnamed: D6.1 (K), J6.1, R4.2, U4.5 (-IN)
unnamed: D7.2 (A), J7.2, Q4.1 (D)
unnamed: D7.1 (K), J7.1, R1.2, U5.5 (-IN)
unnamed: D8.2 (A), R8.2
unnamed: D9.2 (A), R9.2
PWM_1: Q1.2 (G), U1.21 (PA11)
PWM_2: Q2.2 (G), U1.20 (PA10)
PWM_3: Q3.2 (G), U1.18 (PA8)
PWM_4: Q4.2 (G), U1.19 (PA9)
Reset_Buton: C1.1, J4.12, SW1.1, U1.4 (NRST)
SWDCK: J4.6, U1.24 (PA14)
SWDIO: J4.4, U1.23 (PA13)
Start_Buton: SW2.1, U1.22 (PA12)
USART2_RX: J4.13, U1.9 (PA3)
USART2_TX: J4.14, U1.8 (PA2)
VCC: C11.1, J8.1, R1.1, R4.1, R6.1, R7.1, R8.1, U2.4 (+IN), U3.4 (+IN), U4.4 (+IN), U5.4 (+IN), U6.3 (VI)

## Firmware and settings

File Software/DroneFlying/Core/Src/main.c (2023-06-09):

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
/* Includes ------------------------------------------------------------------*/
#include "main.h"
#include "i2c.h"
#include "tim.h"
#include "gpio.h"

/* USER CODE BEGIN PD */
#define UARTTXSIZE 32
#define MPU6050_ADDR 0xD0
#define SMPLRT_DIV_REG 0x19
#define GYRO_CONFIG_REG 0x1B
#define ACCEL_CONFIG_REG 0x1C
#define ACCEL_XOUT_H_REG 0x3B
#define TEMP_OUT_H_REG 0x41
#define GYRO_XOUT_H_REG 0x43
#define PWR_MGMT_1_REG 0x6B
#define WHO_AM_I_REG 0x75

/* USER CODE END PD */


/* USER CODE BEGIN PV */
uint8_t timFlagIt = 0;
float x,y,z;
char uartTxBuffer[UARTTXSIZE];
uint8_t sizeStr;
uint8_t check;
/* USER CODE END PV */

void SystemClock_Config(void);
/**
  * @brief  The application entry point.
  * @retval int
  */
int main(void)
{
  /* MCU Configuration--------------------------------------------------------*/

  /* Reset of all peripherals, Initializes the Flash interface and the Systick. */
  HAL_Init();

  /* Configure the system clock */
  SystemClock_Config();

  /* Initialize all configured peripherals */
  MX_GPIO_Init();
  MX_TIM1_Init(); //Timer used here to set a PWM for controlling the motors.
  MX_TIM6_Init(); //Timer defined to just have a acceptable clock to display on Putty (for Windows) the X,Y,Z acceleration and angular velocity.
  MX_I2C1_Init(); //I2C port used here to communicate (and especially read) information received by

  /* USER CODE BEGIN 2 */
	HAL_TIM_Base_Start_IT(&htim6);
	HAL_TIM_PWM_Start(&htim1, TIM_CHANNEL_1); //Start the PWM we wanted for each motor.
	HAL_TIM_PWM_Start(&htim1, TIM_CHANNEL_2);
	HAL_TIM_PWM_Start(&htim1, TIM_CHANNEL_3);
	HAL_TIM_PWM_Start(&htim1, TIM_CHANNEL_4);
	__HAL_TIM_SET_COMPARE(&htim1, TIM_CHANNEL_1, 800); //Function already implemented in HAL library and allows to compare to a variable CCR (here 800, choosed by myself) and get the exact duty cycle we wanted.
	__HAL_TIM_SET_COMPARE(&htim1, TIM_CHANNEL_2, 600);
	__HAL_TIM_SET_COMPARE(&htim1, TIM_CHANNEL_3, 400);
	__HAL_TIM_SET_COMPARE(&htim1, TIM_CHANNEL_4, 200);
	/* USER CODE BEGIN 2 */
	//Init MPU6050
	HAL_I2C_Mem_Read(&hi2c1, MPU6050_ADDR, WHO_AM_I_REG, 1, &check, 1, 1000);
	if (check == 0x68)  // 0x68 will be returned by the sensor if everything goes well according to the DataSheet
	{
		uint8_t Data;
		// power management register 0X6B we should write all 0's to wake the sensor up
		Data = 0;
		HAL_I2C_Mem_Write(&hi2c1, MPU6050_ADDR, PWR_MGMT_1_REG, 1,&Data, 1, 1000);

		// Set DATA RATE of 1KHz by writing SMPLRT_DIV register
		Data = 0x07;
		HAL_I2C_Mem_Write(&hi2c1, MPU6050_ADDR, SMPLRT_DIV_REG, 1, &Data, 1, 1000);

		// Set accelerometer configuration in ACCEL_CONFIG Register
		// XA_ST=0,YA_ST=0,ZA_ST=0, FS_SEL=0 -> ± 2g
		Data = 0x00;
		HAL_I2C_Mem_Write(&hi2c1, MPU6050_ADDR, ACCEL_CONFIG_REG, 1, &Data, 1, 1000);

		// Set Gyroscopic configuration in GYRO_CONFIG Register
		// XG_ST=0,YG_ST=0,ZG_ST=0, FS_SEL=0 -> ± 250 °/s
		Data = 0x00;
		HAL_I2C_Mem_Write(&hi2c1, MPU6050_ADDR, GYRO_CONFIG_REG, 1, &Data, 1, 1000);
	}
  /* USER CODE END 2 */

  /* Infinite loop */
  /* USER CODE BEGIN WHILE */
	while (1)
	{
    /* USER CODE END WHILE */

    /* USER CODE BEGIN 3 */
		if(timFlagIt){
			uint8_t Rec_Data[6];
			int16_t Accel_X_RAW = 0; //We define a Rec_Data array to stock data
			int16_t Accel_Y_RAW = 0; //received from the MPU6050 in variables
			int16_t Accel_Z_RAW = 0; //Accel_X_RAW, Accel_Y_RAW and Accel_Z_RAW which are 16bits signed integer (int16_t).
			HAL_I2C_Mem_Read (&hi2c1, MPU6050_ADDR, ACCEL_XOUT_H_REG, 1, Rec_Data, 6, 1000);

			Accel_X_RAW = (int16_t)(Rec_Data[0] << 8 | Rec_Data [1]);
			Accel_Y_RAW = (int16_t)(Rec_Data[2] << 8 | Rec_Data [3]);
			Accel_Z_RAW = (int16_t)(Rec_Data[4] << 8 | Rec_Data [5]);

			x = Accel_X_RAW/16384.0; //Same here. But we divide by 16384.0 to obtain acceleration values in gravity units (in g).
			y = Accel_Y_RAW/16384.0; //snprintf is used to format the values of x, y, and z into a string and stores it in uartTxBuffer
			z = Accel_Z_RAW/16384.0;


			sizeStr = snprintf(uartTxBuffer, UARTTXSIZE, "X=%1.3f, Y=%1.3f, Z=%1.3f\r\n",x,y,z);
			int16_t Accel_PHI_RAW = 0;
			int16_t Accel_THETA_RAW = 0;
			int16_t Accel_PSI_RAW = 0;
			HAL_I2C_Mem_Read (&hi2c1, MPU6050_ADDR, GYRO_XOUT_H_REG, 1, Rec_Data, 6, 1000);

			Accel_PHI_RAW = (int16_t)(Rec_Data[0] << 8 | Rec_Data [1]); //Same here to get the angular velocity.
			Accel_THETA_RAW = (int16_t)(Rec_Data[2] << 8 | Rec_Data [3]);
			Accel_PSI_RAW = (int16_t)(Rec_Data[4] << 8 | Rec_Data [5]);

			float PHI = Accel_PHI_RAW/16384.0;
			float THETA = Accel_THETA_RAW/16384.0;
			float PSI = Accel_PSI_RAW/16384.0;

			sizeStr = snprintf(uartTxBuffer, UARTTXSIZE, "PHI=%1.3f, THETA=%1.3f, PSI=%1.3f\r\n",PHI,THETA,PSI);
//			HAL_UART_Transmit(&huart1, uartTxBuffer, sizeStr, 100); //the string is transmitted over UART using HAL.

		timFlagIt = 0; //Making sure the loop does work properly.
		}
	}
  /* USER CODE END 3 */
}

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
/* USER CODE BEGIN 4 */
void HAL_TIM_PeriodElapsedCallback(TIM_HandleTypeDef *htim)
{
	HAL_GPIO_TogglePin(LD1_GPIO_Port, LD1_Pin);
	timFlagIt = 1;
}
//This function is a callback function to deal with interuptions of the clock in the process.
/* USER CODE END 4 */
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


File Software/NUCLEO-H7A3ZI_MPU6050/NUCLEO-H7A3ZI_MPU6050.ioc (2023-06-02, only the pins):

Mcu.UserName=STM32H7A3ZITxQ
PA10.GPIO_Label=USB_FS_ID [ZX62RD-AB-5P8_ID]
PA10.Signal=USB_OTG_HS_ID
PA11.GPIO_Label=USB_FS_N [USBLC6-2SC6_IO_1]
PA11.Signal=USB_OTG_HS_DM
PA12.GPIO_Label=USB_FS_P [USBLC6-2SC6_IO_2]
PA12.Signal=USB_OTG_HS_DP
PA9.GPIO_Label=USB_FS_VBUS  [ZX62RD-AB-5P8_VBUS]
PA9.Signal=USB_OTG_HS_VBUS
PB0.GPIO_Label=LD1 (Green Led)
PB0.Signal=GPIO_Output
PB14.GPIO_Label=LD3 (Red Led)
PB14.Signal=GPIO_Output
PB6.Signal=I2C1_SCL
PB7.Signal=I2C1_SDA
PC13.GPIO_Label=B1 (Blue PushButton)
PC13.Signal=GPIO_Input
PC14-OSC32_IN.GPIO_Label=OSC32_IN
PC14-OSC32_IN.Signal=RCC_OSC32_IN
PC15-OSC32_OUT.GPIO_Label=OSC32_OUT
PC15-OSC32_OUT.Signal=RCC_OSC32_OUT
PD8.GPIO_Label=STLINK_RX
PD8.Signal=USART3_TX
PD9.GPIO_Label=STLINK_TX
PD9.Signal=USART3_RX
PE1.GPIO_Label=LD2 (Yellow Led)
PE1.Signal=GPIO_Output
PE11.Signal=S_TIM1_CH2
PE13.Signal=S_TIM1_CH3
PE14.Signal=S_TIM1_CH4
PE9.Signal=S_TIM1_CH1
PF10.GPIO_Label=USB_FS_PWR_EN [STMPS2141STR_EN]
PF10.Signal=GPIO_Output
PG7.GPIO_Label=USB_FS_OVCR  [STMPS2141STR_FAULT]
PG7.Signal=GPXTI7
PH0-OSC_IN.GPIO_Label=PH0-MCU
PH0-OSC_IN.Signal=RCC_OSC_IN
PH1-OSC_OUT.GPIO_Label=PH1-MCU
PH1-OSC_OUT.Signal=RCC_OSC_OUT

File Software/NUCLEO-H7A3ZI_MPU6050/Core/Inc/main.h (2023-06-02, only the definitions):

#define B1_Pin GPIO_PIN_13
#define B1_GPIO_Port GPIOC
#define OSC32_IN_Pin GPIO_PIN_14
#define OSC32_IN_GPIO_Port GPIOC
#define OSC32_OUT_Pin GPIO_PIN_15
#define OSC32_OUT_GPIO_Port GPIOC
#define USB_FS_PWR_EN_Pin GPIO_PIN_10
#define USB_FS_PWR_EN_GPIO_Port GPIOF
#define PH0_MCU_Pin GPIO_PIN_0
#define PH0_MCU_GPIO_Port GPIOH
#define PH1_MCU_Pin GPIO_PIN_1
#define PH1_MCU_GPIO_Port GPIOH
#define LD1_Pin GPIO_PIN_0
#define LD1_GPIO_Port GPIOB
#define LD3_Pin GPIO_PIN_14
#define LD3_GPIO_Port GPIOB
#define STLINK_RX_Pin GPIO_PIN_8
#define STLINK_RX_GPIO_Port GPIOD
#define STLINK_TX_Pin GPIO_PIN_9
#define STLINK_TX_GPIO_Port GPIOD
#define USB_FS_OVCR_Pin GPIO_PIN_7
#define USB_FS_OVCR_GPIO_Port GPIOG
#define USB_FS_VBUS_Pin GPIO_PIN_9
#define USB_FS_VBUS_GPIO_Port GPIOA
#define USB_FS_ID_Pin GPIO_PIN_10
#define USB_FS_ID_GPIO_Port GPIOA
#define USB_FS_N_Pin GPIO_PIN_11
#define USB_FS_N_GPIO_Port GPIOA
#define USB_FS_P_Pin GPIO_PIN_12
#define USB_FS_P_GPIO_Port GPIOA
#define LD2_Pin GPIO_PIN_1
#define LD2_GPIO_Port GPIOE

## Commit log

2023-04-03 Ajout du diagramme PCB
2023-04-11 Ajouté(e) PWM
2023-04-11 Mettre à jour PWM
2023-04-15 pcb schematic sans erreur et editeur sans erreur egalement
    [PCBschematic.kicad_pcb, PCBschematic.kicad_sch, untitled.kicad_sch]
2023-04-15 ajout des GND sur le pcb
    [PCBschematic.kicad_pcb]
2023-04-17 pcb en cours de correction
    [PCBschematic.kicad_pcb, PCBschematic.kicad_sch, untitled.kicad_sch]
2023-04-22 pcb_mise_en_place_okay_reste_3_erreurs git commit -m pcb_mise_en_place_okay_reste_3_erreurs
    [PCBschematic.kicad_pcb]
2023-04-25 modif pcb
    [PCBschematic.kicad_pcb]
2023-05-02 routage v1
    [PCBschematic.kicad_pcb]
2023-05-09 Update PCB Schem + Objectif dev durable
2023-05-13 nouveau pcb
    [PCBschematic.kicad_pcb]
2023-05-15 routage v2
    [PCBschematic.kicad_pcb]
2023-05-16 Update PWM
2023-05-19 add pcb with bigger vias
    [PCBschematic.csv, PCBschematic.kicad_pcb, PCBschematic.kicad_sch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]
2023-05-25 code MPU GYRO
2023-05-26 Update MPU6050 and PWM
2023-05-30 PWM works now
2023-06-01 Ajouté(e) fonctions PWM.drawio
2023-06-01 Mettre à jour fonctions PWM.drawio
2023-06-02 Update software and adding STM32 project
2023-06-02 Ajout de texte au CR
2023-06-02 reorganisation des fichiers et des dossiers
2023-06-02 ajout des URLS des photos pour le Cr
2023-06-02 fin ajout images partie PCB
2023-06-04 ajout description composants sur schématique
    [PCBschematic.kicad_sch, untitled.kicad_sch]
2023-06-09 Update for LDO/Découpage regulator differences

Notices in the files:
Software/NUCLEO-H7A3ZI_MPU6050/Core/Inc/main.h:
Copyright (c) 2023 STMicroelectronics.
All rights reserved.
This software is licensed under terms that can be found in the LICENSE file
